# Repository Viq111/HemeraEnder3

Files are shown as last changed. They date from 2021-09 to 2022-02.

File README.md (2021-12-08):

# Hemera on Ender 3

Hello! This repo should (hopefully) help you put an Hemera onto an Ender 3 Pro in the year 2021 in a breeze.
I mostly created this because I was following [Hemera to Ender 3 - Complete guide](https://www.youtube.com/watch?v=oY1F7fUBHrc) but some information was outdated; hopefully this will help one or two people in the future.

This is not meant to be a complete guide but a diff to the [video above](https://www.youtube.com/watch?v=oY1F7fUBHrc) so you should go watch it first and then come back here.

As a headsup, you can definitely do the installation in three steps: first the Hemera, second adding the part-cooling fan (I still had great success without a part cooling fan at first), third the BLTouch.

## (Better) Parts to print + additional hardware

Contrary to the video, I feel like the two part build is pretty heavy and make you loose a lot of space for no reason.
I actually used the part from [E3D hemera Mount and cooler for Cr-10 and Ender 3 by Tragical](https://www.thingiverse.com/thing:4061250) which are much better and do not make you loose any build volume.
You'll find bellow (quick links to the `stl` folder) some remixed versions.

### What you need to print:
- [`HemeraMount.stl` STL](https://github.com/Viq111/HemeraEnder3/blob/master/stl/HemeraMount.stl) ( remix to make the BLTouch mount nut slots a bit bigger so it's easy to use even with shrinking (at the end of the day, you don't need something snug))
- [`PartFan.stl` STL](https://github.com/Viq111/HemeraEnder3/blob/master/stl/PartFan.stl) + [`PartFanArm.stl` STL](https://github.com/Viq111/HemeraEnder3/blob/master/stl/PartFanArm.stl)
- [`BLTouchMount.stl` STL](https://github.com/Viq111/HemeraEnder3/blob/master/stl/BLTouchMount.stl) (completely changed from original to not bumps into the Y axis motor without triggering the end switch)
You need to add a support enforcer when printing as show [here](https://github.com/Viq111/HemeraEnder3/blob/master/stl/BLTouchMountSupport.png)

### Additional hardware:

**Fan mount:**
- 2x M4 hex nuts
- 2x M4x22mm screws (if you want to be safe and not do back&forth to the store, also get some M4x20mm & M4x25mm, you can always reuse in the future)

**BLTouch mount:**
- 4x M3 hex nuts
- 4x M3x10mm

### Final result:

Once mounted it should look like this!
final

## Vref calibration

I couldn't find easily the documentation online about what is Vref, Irms (sometimes just called RMS) so I'm doing a full section on it so it's clear for you.
Vref calibration is actually pretty simple and you don't have to be very precise! It basically just set the upper limit on what current you can send to your stepper motor without blowing it.

What you need first:
- Know the motor drivers you have on your board (for me with a Creality Silent Board 1.1.5, that was TMC2208)
- Know the "Rsense" value installed on your board. You can look this up online or directly on your board (the resistance close to where you plug the E stepper motor should have a number on it). Most of the time, it should be "100" which is a 0.100 Ohm resistance. For me on the Creality Silent Board 1.1.5, Rsense=150

You then can refer to the [Hemera documentation](https://e3d-online.zendesk.com/hc/en-us/articles/360016249057-Hemera-Current-Adjustment-PDF-) ([alternate link if down](https://github.com/Viq111/HemeraEnder3/files/7080832/Hemera.Current.Adjustments.pdf))

For me with TMC2208, it will tell you to use Irms (which is basically max current divided by square root of 2 with some formula)
What's really not clear here is the computation is actually just a cross product which tells you at 2.5V, your driver will deliver x amp.
Refer to the driver's documentation to try to find that value. For TMC2208, the documentation is [here](https://github.com/Viq111/HemeraEnder3/files/7080838/TMC220x_TMC2224_datasheet_Rev1.09.pdf). Page 49, you can see with Rsense=100, Vref=2.5V => Irms = 1.77A. With Rsense=150, Vref=2.5V => Irms = 1.28A.

The Hemera should be driven with a max Irms= 1.33A*sqtr(2) = 0.94A.
With Rsense=150, I want 0.94A and for Vref=2.5V,Irms=1.28A. With a cross product, that gives me Vref = Irms_want / Irms_at_2.5 * 2.5V = 1.83V.
That's the **maximum** value you can ever set your Vref at before you burn your stepper motor.
It is recommended to set a value at ~80-90% of that maximum value to be safe. I initially set it to the value in the video (0.5V) and that definitely didn't work so I would recommend not setting it to < 70% max value.
As you can see, Vref doesn't actually need to be accurate, you can set it anywhere between 70% & 90% of you max value. In my case (Creality Silent Board 1.1.5), I want to set it between 1.28V & 1.65V.

Remember that:
- If you set your Vref too high, you can break your stepper motor so always do the computation and that will give you the upper bound
- If you set your Vref too low, your motor won't move or "skip steps" (so basically not extrude correctly). Since I never had a stepper motor overhead, I set mine at 90% of max and it has been doing fine.

tl; dr; Don't change Vref except if you run into issues. The stock value works except if the new stepper is 2x more powerful than previously. The Hemera stepper motor should be more powerful than the stock one so no risk of damaging it.

## Marlin 2 config

### Bootloader

I don't remember too much this step so I won't go too much into details. If you have an arduino, there should be plenty of guides. If you use the Creality BLTouch kit, you can follow this [reddit thread](https://www.reddit.com/r/ender3/comments/cfmbdy/howto_installing_a_bootloader_to_an_ender_3_pro/).

Two things worth mentioning:
- The `DC, D6, FD and FF` values are **correct** (opposite of what's in the BLTouch kit guide), this is because you are flashing the **bootloader and not the firmware**.
- There is one step not mentioned in the guide: you need to select the correct microprocessor that is on your board

After you have succesfully flashed the bootloader, you'll be able to repeatedly flash the firmware with an attached Octoprint (or similar) 

### Config

1. Download the latest firmware from https://github.com/MarlinFirmware/Marlin/releases
1. Download the correct config from https://github.com/MarlinFirmware/Configurations and override the `Configuration.h` and `Configuration_adv.h` with files for your printer
1. You can modify the values as shown in this commit: https://github.com/Viq111/HemeraEnder3/commit/fd97170 (make sure to set the correct driver for the board you are using, you can also look at the other commits)
1. Use VS Code & PlatformIO to build (don't use Arduino IDE, that has been deprecated and is hard to get it working now)

Now you should have a working Ender 3 with a Hemera hotend!
A fully working copy of  Marlin is also available in the `Marlin` folder of this repository

### Adding BLTouch

If you used the M206 to set your home previously, with the BLTouch you will need to actually (physically) modify your end stops as [M206 doesn't work for the BLTouch](https://github.com/MarlinFirmware/Marlin/issues/17158). Once you have set them, don't forget to reset your M206 to zero.

On the software side, you will want to pick this [additional configuration](https://github.com/Viq111/HemeraEnder3/commit/ab540f3).

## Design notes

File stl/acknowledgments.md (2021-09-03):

All parts are from [E3D hemera Mount and cooler for Cr-10 and Ender 3 by Tragical](https://www.thingiverse.com/thing:4061250) except mentioned otherwise

- `BLTouchMount.stl`: I designed from scratch (and my measurements) but after trying the one from the pack above so there is some inspiration from there.
- `HemeraMount.stl` is from the pack, I only increased the size of the holes for the hex nut for the BLTouch mount.
- `PartFan.stl` is unmodified. Print it with the arms up.
- `PartFanArm.stl` is unmodified. Print it with the hex nut slots facing up.

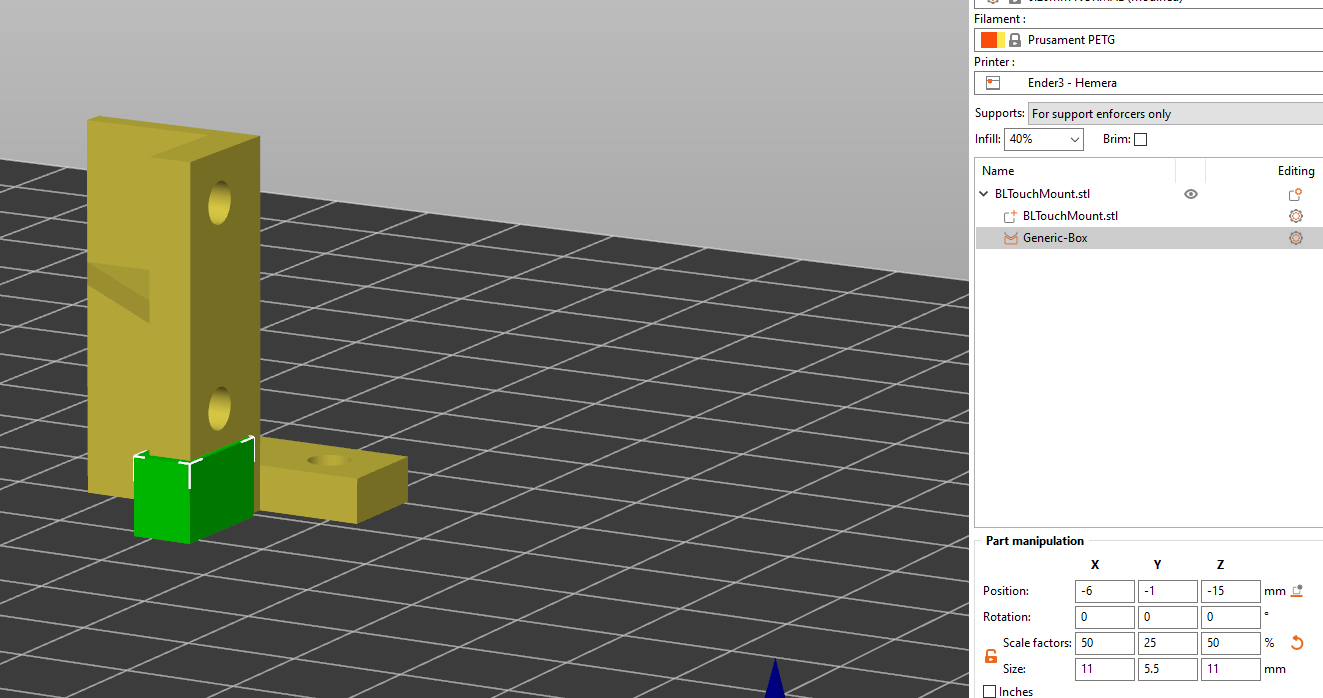
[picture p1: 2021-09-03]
stl/BLTouchMountSupport.png

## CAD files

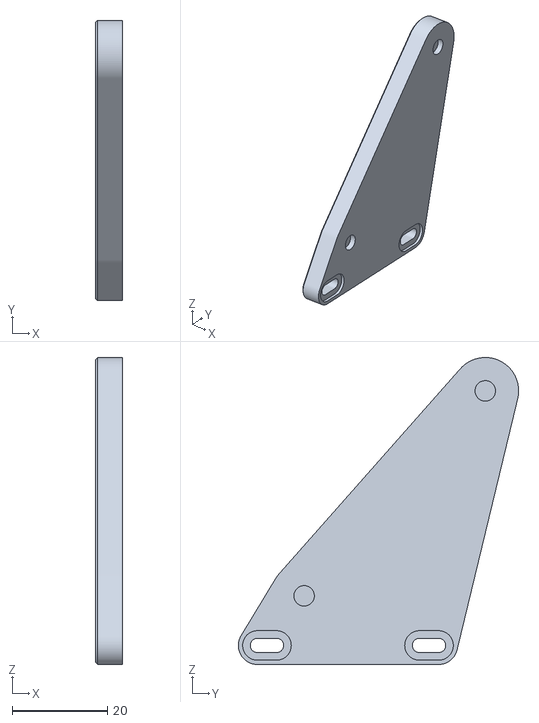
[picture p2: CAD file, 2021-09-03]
stl/PartFanArm.stl
5.60 x 58.8 x 64.4

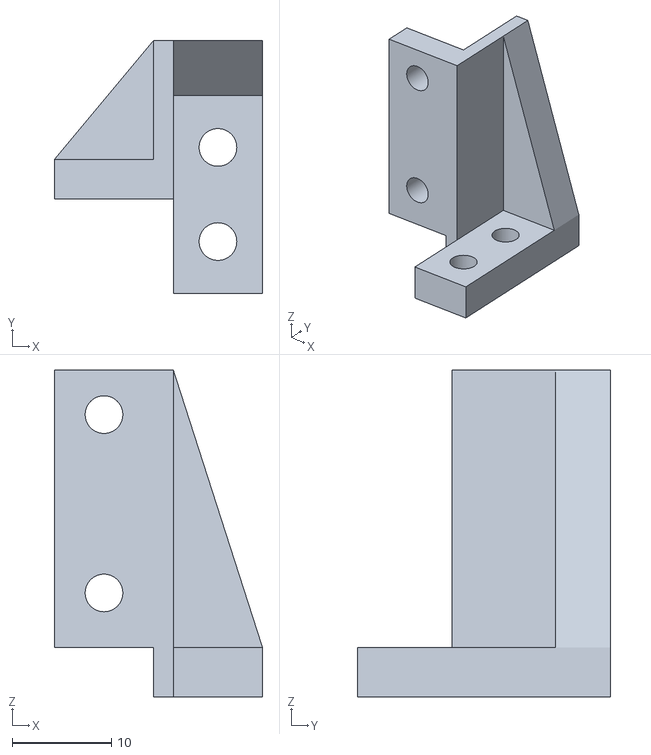
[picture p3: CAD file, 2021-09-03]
stl/BLTouchMount.stl
21.0 x 25.6 x 33.0

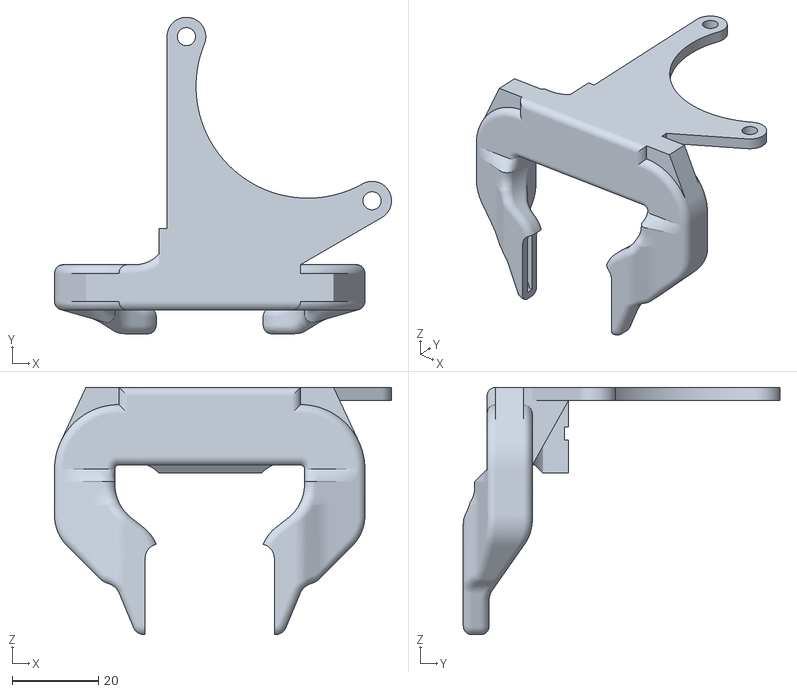
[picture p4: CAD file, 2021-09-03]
stl/PartFan.stl
78.0 x 73.3 x 57.3

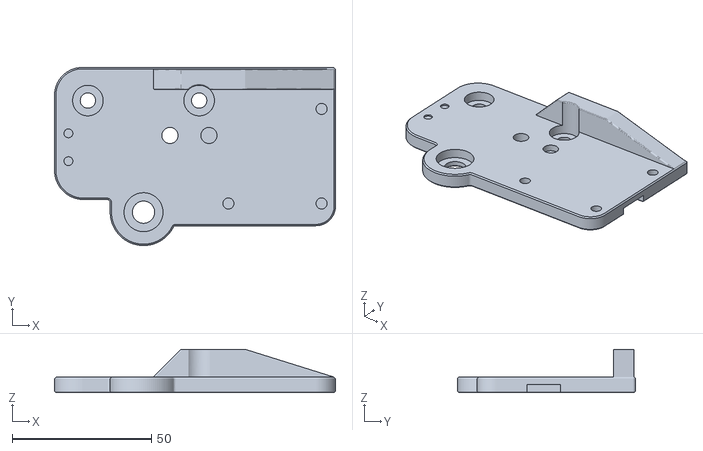
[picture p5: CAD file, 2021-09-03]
stl/HemeraMount.stl
101.0 x 64.0 x 15.6

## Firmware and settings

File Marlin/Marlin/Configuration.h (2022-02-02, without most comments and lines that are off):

#pragma once
#define CONFIG_EXAMPLES_DIR "Creality/Ender-3 Pro/CrealityV1"
#define CONFIGURATION_H_VERSION 02000903
#define STRING_CONFIG_H_AUTHOR "(thisiskeithb, Ender-3 Pro)" // Who made the changes.
#define SHOW_BOOTSCREEN
#define SHOW_CUSTOM_BOOTSCREEN
#define CUSTOM_STATUS_SCREEN_IMAGE
  #define MOTHERBOARD BOARD_MELZI_CREALITY
#define SERIAL_PORT 0
#define BAUDRATE 115200
#define CUSTOM_MACHINE_NAME "Ender-3 Pro"
#if LINEAR_AXES >= 4
  #define AXIS4_NAME 'A' // :['A', 'B', 'C', 'U', 'V', 'W']
#endif
#if LINEAR_AXES >= 5
  #define AXIS5_NAME 'B' // :['A', 'B', 'C', 'U', 'V', 'W']
#endif
#if LINEAR_AXES >= 6
  #define AXIS6_NAME 'C' // :['A', 'B', 'C', 'U', 'V', 'W']
#endif
#define EXTRUDERS 1
#define DEFAULT_NOMINAL_FILAMENT_DIA 1.75
#define TEMP_SENSOR_0 5
#define TEMP_SENSOR_1 0
#define TEMP_SENSOR_2 0
#define TEMP_SENSOR_3 0
#define TEMP_SENSOR_4 0
#define TEMP_SENSOR_5 0
#define TEMP_SENSOR_6 0
#define TEMP_SENSOR_7 0
#define TEMP_SENSOR_BED 1
#define TEMP_SENSOR_PROBE 0
#define TEMP_SENSOR_CHAMBER 0
#define TEMP_SENSOR_COOLER 0
#define TEMP_SENSOR_BOARD 0
#define TEMP_SENSOR_REDUNDANT 0
#define DUMMY_THERMISTOR_998_VALUE  25
#define DUMMY_THERMISTOR_999_VALUE 100
#define TEMP_RESIDENCY_TIME         10  // (seconds) Time to wait for hotend to "settle" in M109
#define TEMP_WINDOW                  1  // (°C) Temperature proximity for the "temperature reached" timer
#define TEMP_HYSTERESIS              3  // (°C) Temperature proximity considered "close enough" to the target
#define TEMP_BED_RESIDENCY_TIME     10  // (seconds) Time to wait for bed to "settle" in M190
#define TEMP_BED_WINDOW              1  // (°C) Temperature proximity for the "temperature reached" timer
#define TEMP_BED_HYSTERESIS          3  // (°C) Temperature proximity considered "close enough" to the target
#define TEMP_CHAMBER_RESIDENCY_TIME 10  // (seconds) Time to wait for chamber to "settle" in M191
#define TEMP_CHAMBER_WINDOW          1  // (°C) Temperature proximity for the "temperature reached" timer
#define TEMP_CHAMBER_HYSTERESIS      3  // (°C) Temperature proximity considered "close enough" to the target
#if TEMP_SENSOR_REDUNDANT
  #define TEMP_SENSOR_REDUNDANT_SOURCE    E1  // The sensor that will provide the redundant reading.
  #define TEMP_SENSOR_REDUNDANT_TARGET    E0  // The sensor that we are providing a redundant reading for.
  #define TEMP_SENSOR_REDUNDANT_MAX_DIFF  10  // (°C) Temperature difference that will trigger a print abort.
#endif
#define HEATER_0_MINTEMP   5
#define HEATER_1_MINTEMP   5
#define HEATER_2_MINTEMP   5
#define HEATER_3_MINTEMP   5
#define HEATER_4_MINTEMP   5
#define HEATER_5_MINTEMP   5
#define HEATER_6_MINTEMP   5
#define HEATER_7_MINTEMP   5
#define BED_MINTEMP        5
#define CHAMBER_MINTEMP    5
#define HEATER_0_MAXTEMP 300
#define HEATER_1_MAXTEMP 275
#define HEATER_2_MAXTEMP 275
#define HEATER_3_MAXTEMP 275
#define HEATER_4_MAXTEMP 275
#define HEATER_5_MAXTEMP 275
#define HEATER_6_MAXTEMP 275
#define HEATER_7_MAXTEMP 275
#define BED_MAXTEMP      125
#define CHAMBER_MAXTEMP  60
#define HOTEND_OVERSHOOT 15   // (°C) Forbid temperatures over MAXTEMP - OVERSHOOT
#define BED_OVERSHOOT    10   // (°C) Forbid temperatures over MAXTEMP - OVERSHOOT
#define COOLER_OVERSHOOT  2   // (°C) Forbid temperatures closer than OVERSHOOT
#define PIDTEMP
#define BANG_MAX 255     // Limits current to nozzle while in bang-bang mode; 255=full current
#define PID_MAX BANG_MAX // Limits current to nozzle while PID is active (see PID_FUNCTIONAL_RANGE below); 255=full current
#define PID_K1 0.95      // Smoothing factor within any PID loop
  #define PID_EDIT_MENU           // Add PID editing to the "Advanced Settings" menu. (~700 bytes of PROGMEM)
  #define PID_AUTOTUNE_MENU       // Add PID auto-tuning to the "Advanced Settings" menu. (~250 bytes of PROGMEM)
    #define DEFAULT_Kp  23.75
    #define DEFAULT_Ki   1.89
    #define DEFAULT_Kd  74.41
#define MAX_BED_POWER 255 // limits duty cycle to bed; 255=full current
#define MAX_CHAMBER_POWER 255 // limits duty cycle to chamber heater; 255=full current
  #define PID_FUNCTIONAL_RANGE 10 // If the temperature difference between the target temperature and the actual temperature
#define PREVENT_COLD_EXTRUSION
#define EXTRUDE_MINTEMP 170
#define PREVENT_LENGTHY_EXTRUDE
#define EXTRUDE_MAXLENGTH 200
#define THERMAL_PROTECTION_HOTENDS // Enable thermal protection for all extruders
#define THERMAL_PROTECTION_BED     // Enable thermal protection for the heated bed
#define THERMAL_PROTECTION_CHAMBER // Enable thermal protection for the heated chamber
#define THERMAL_PROTECTION_COOLER  // Enable thermal protection for the laser cooling
#define USE_XMIN_PLUG
#define USE_YMIN_PLUG
#define USE_ZMIN_PLUG
#define ENDSTOPPULLUPS
#define X_MIN_ENDSTOP_INVERTING false // Set to true to invert the logic of the endstop.
#define Y_MIN_ENDSTOP_INVERTING false // Set to true to invert the logic of the endstop.
#define Z_MIN_ENDSTOP_INVERTING false // Set to true to invert the logic of the endstop.
#define I_MIN_ENDSTOP_INVERTING false // Set to true to invert the logic of the endstop.
#define J_MIN_ENDSTOP_INVERTING false // Set to true to invert the logic of the endstop.
#define K_MIN_ENDSTOP_INVERTING false // Set to true to invert the logic of the endstop.
#define X_MAX_ENDSTOP_INVERTING false // Set to true to invert the logic of the endstop.
#define Y_MAX_ENDSTOP_INVERTING false // Set to true to invert the logic of the endstop.
#define Z_MAX_ENDSTOP_INVERTING false // Set to true to invert the logic of the endstop.
#define I_MAX_ENDSTOP_INVERTING false // Set to true to invert the logic of the endstop.
#define J_MAX_ENDSTOP_INVERTING false // Set to true to invert the logic of the endstop.
#define K_MAX_ENDSTOP_INVERTING false // Set to true to invert the logic of the endstop.
#define Z_MIN_PROBE_ENDSTOP_INVERTING false // Set to true to invert the logic of the probe.
#define X_DRIVER_TYPE  TMC2208_STANDALONE
#define Y_DRIVER_TYPE  TMC2208_STANDALONE
#define Z_DRIVER_TYPE  TMC2208_STANDALONE
#define E0_DRIVER_TYPE TMC2208_STANDALONE
#define DEFAULT_AXIS_STEPS_PER_UNIT   { 80, 80, 400, 400 }
#define DEFAULT_MAX_FEEDRATE          { 500, 500, 5, 25 }
#define DEFAULT_MAX_ACCELERATION      { 500, 500, 100, 5000 }
#define DEFAULT_ACCELERATION          500    // X, Y, Z and E acceleration for printing moves
#define DEFAULT_RETRACT_ACCELERATION  500    // E acceleration for retracts
#define DEFAULT_TRAVEL_ACCELERATION   500    // X, Y, Z acceleration for travel (non printing) moves
#define DEFAULT_EJERK    5.0  // May be used by Linear Advance
  #define JUNCTION_DEVIATION_MM 0.08  // (mm) Distance from real junction edge
  #define JD_HANDLE_SMALL_SEGMENTS    // Use curvature estimation instead of just the junction angle
#define Z_MIN_PROBE_USES_Z_MIN_ENDSTOP_PIN
#define USE_PROBE_FOR_Z_HOMING
#define BLTOUCH
#define NOZZLE_TO_PROBE_OFFSET { -54, -3, 0 }
#define PROBING_MARGIN 10
#define XY_PROBE_FEEDRATE (133*60)
#define Z_PROBE_FEEDRATE_FAST (4*60)
#define Z_PROBE_FEEDRATE_SLOW (Z_PROBE_FEEDRATE_FAST / 2)
#define Z_CLEARANCE_DEPLOY_PROBE   10 // Z Clearance for Deploy/Stow
#define Z_CLEARANCE_BETWEEN_PROBES  5 // Z Clearance between probe points
#define Z_CLEARANCE_MULTI_PROBE     5 // Z Clearance between multiple probes
#define Z_PROBE_LOW_POINT          -2 // Farthest distance below the trigger-point to go before stopping
#define Z_PROBE_OFFSET_RANGE_MIN -20
#define Z_PROBE_OFFSET_RANGE_MAX 20
#define X_ENABLE_ON 0
#define Y_ENABLE_ON 0
#define Z_ENABLE_ON 0
#define E_ENABLE_ON 0 // For all extruders
#define DISABLE_X false
#define DISABLE_Y false
#define DISABLE_Z false
#define DISABLE_E false             // Disable the extruder when not stepping
#define INVERT_X_DIR true
#define INVERT_Y_DIR true
#define INVERT_Z_DIR false
#define INVERT_E0_DIR true
#define INVERT_E1_DIR false
#define INVERT_E2_DIR false
#define INVERT_E3_DIR false
#define INVERT_E4_DIR false
#define INVERT_E5_DIR false
#define INVERT_E6_DIR false
#define INVERT_E7_DIR false
#define X_HOME_DIR -1
#define Y_HOME_DIR -1
#define Z_HOME_DIR -1
#define X_BED_SIZE 230
#define Y_BED_SIZE 230
#define X_MIN_POS 0
#define Y_MIN_POS 0
#define Z_MIN_POS 0
#define X_MAX_POS X_BED_SIZE
#define Y_MAX_POS Y_BED_SIZE
#define Z_MAX_POS 200
#define MIN_SOFTWARE_ENDSTOPS
  #define MIN_SOFTWARE_ENDSTOP_X
  #define MIN_SOFTWARE_ENDSTOP_Y
  #define MIN_SOFTWARE_ENDSTOP_Z
  #define MIN_SOFTWARE_ENDSTOP_I
  #define MIN_SOFTWARE_ENDSTOP_J
  #define MIN_SOFTWARE_ENDSTOP_K
#define MAX_SOFTWARE_ENDSTOPS
  #define MAX_SOFTWARE_ENDSTOP_X
  #define MAX_SOFTWARE_ENDSTOP_Y
  #define MAX_SOFTWARE_ENDSTOP_Z
  #define MAX_SOFTWARE_ENDSTOP_I
  #define MAX_SOFTWARE_ENDSTOP_J
  #define MAX_SOFTWARE_ENDSTOP_K
#define AUTO_BED_LEVELING_BILINEAR
#define PREHEAT_BEFORE_LEVELING
  #define LEVELING_NOZZLE_TEMP 120   // (°C) Only applies to E0 at this time
  #define LEVELING_BED_TEMP     60
  #define ENABLE_LEVELING_FADE_HEIGHT
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

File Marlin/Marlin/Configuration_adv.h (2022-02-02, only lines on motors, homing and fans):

#define E0_AUTO_FAN_PIN -1
#define E1_AUTO_FAN_PIN -1
#define E2_AUTO_FAN_PIN -1
#define E3_AUTO_FAN_PIN -1
#define E4_AUTO_FAN_PIN -1
#define E5_AUTO_FAN_PIN -1
#define E6_AUTO_FAN_PIN -1
#define E7_AUTO_FAN_PIN -1
#define CHAMBER_AUTO_FAN_PIN -1
#define COOLER_AUTO_FAN_PIN -1
#define COOLER_FAN_PIN -1
#define HOMING_BUMP_MM      { 5, 5, 2 }       // (mm) Backoff from endstops after first bump
#define HOMING_BUMP_DIVISOR { 2, 2, 4 }       // Re-Bump Speed Divisor (Divides the Homing Feedrate)
#define QUICK_HOME                            // If G28 contains XY do a diagonal move first
#define MICROSTEP_MODES { 16, 16, 16, 16, 16, 16 } // [1,2,4,8,16]

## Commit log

2021-09-02 [Marlin] Put into its own subdirectory
    [Configuration.h, Configuration_adv.h]
2021-09-02 [config] Import Ender3ProV1 config
    [Configuration.h, Configuration_adv.h]
2021-09-03 [github] Remove templates from Marlin
2021-09-03 [config] Update for Hemera values
    [Configuration.h, Configuration_adv.h]
2021-09-03 [config] Adjust bed size for Hemera
    [Configuration.h]
2021-09-03 [octoprint] Enable host commands as requested
    [Configuration_adv.h]
2021-09-03 [config] Allow progress to be shown on LCD
    [Configuration_adv.h]
2021-09-03 [config] PID calibration with PETG
    [Configuration.h]
2021-09-03 [stl] Add all the parts
    [BLTouchMount.stl, HemeraMount.stl, PartFan.stl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]
2021-09-03 [config] Enable BLTouch for Hemera
    [Configuration.h, Configuration_adv.h]
2022-01-25 [marlin] Update to 2.0.9.3
    [Configuration.h, Configuration_adv.h, esp32.csv]
2022-01-26 [marlin] Re-apply Ender3 defaults
    [Configuration.h, Configuration_adv.h]
2022-01-26 [marlin] Cherry-pick previous Hemera-specific changes
    Commits:
    [config] Update for Hemera values
    [config] Adjust bed size for Hemera
    [octoprint] Enable host commands as requested
    [config] Allow progress to be shown on LCD
    [config] PID calibration with PETG
    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
    [Configuration.h, Configuration_adv.h]
2022-01-30 [marlin] Additional small touches
    - Enable PREHEAT_BEFORE_PROBING
    - Better default settings for PLA/PETG
    - Enable PRINTCOUNTER
    - Tweak Thermal Protection so it doesn't trigger when fan turns on without a silicone sock
    [Configuration.h, Configuration_adv.h]

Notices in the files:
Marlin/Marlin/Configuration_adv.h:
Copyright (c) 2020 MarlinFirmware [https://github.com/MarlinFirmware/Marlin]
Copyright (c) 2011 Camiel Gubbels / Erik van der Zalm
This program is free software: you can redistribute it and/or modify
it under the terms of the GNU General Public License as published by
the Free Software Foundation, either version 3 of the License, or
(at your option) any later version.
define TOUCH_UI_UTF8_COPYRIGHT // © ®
